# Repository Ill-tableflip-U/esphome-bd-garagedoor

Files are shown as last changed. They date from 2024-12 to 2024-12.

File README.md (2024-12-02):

# esphome B&D garage door configuration

This is how to build a complete pre-designed ESPhome device to interface with a B&D garage door, by simulating button presses on one of the included remotes (specifically a 2012 model)

Material list:
* 1 ESP32-C3 supermini
* A decent amount of wire
* A 5v/USB power source
* access to a 3d printer
optional:
* 1 ws2812 LED
* 1 hc-sr501 motion sensor
the B&D stock remote control can be opened up and modified for control use with ESPhome. for each garage door, the following is needed:
* 1 BC559 PNP transistor
* 1 10K ohm pullup resistor
* 1 1M ohm resistor for the base pin
* 1 reed switch (I recommend https://www.aliexpress.com/item/1005007038721944.html)
These all go inside the shell for the remote and can be directly soldered to it. Keep in mind, this likely only fits with the larger, white remote shells like the one pictured.

remote control modification


In the images, the blue wires are for power to hardwire the remote power along with the ESP. The red and white wires are the control outputs, for controlling the doors.
To modify the controller
1. eject the button cell battery as that will no longer be needed
2. straddle a BC559 transistor onto the side of the board for each button you wish to control. The collector pin should sit on the button solder pad closest to the board edge, meanwhile the emitter pin should be soldered to the pad closest to the center. The middle pin of the transistor (the base) should go onto the back side of the board. 

3. Solder a 1 million ohm resistor to the base pin of the BC559. (You should probably trim the legs of all of these)
4. after the 1m ohm resistor, solder one side of a 10k resistor to the empty end, and the other side to the button cell battery shieldd
5. Solder a ground wire to the 0v pad on the rear of the remote board and a 3.3v wire to the top of the button cell battery receptacle.
6. In the junction between the two resistors, solder a wire and connect it to any esp GPIO. You can now control your garage!

It is fairly easy to drill a small hole in the top of the original remote shell so these wires can be routed to the ESP setup.

Now, 3D print the enclosure for the device, or make your own. Mine, which has a .blend and a .stl available to print, has room for the the necessary hardware for garage doors as well as a ws2812 LED and a hc-SR501 motion sensor and is designed around the ESP32-C3 supermini. This is an effective all-in-one design that seems to work well.

PLEASE NOTE: some ESP32-C3 superminis have bad antenna chips, I used one of those for this project and it turned out fine. Still, YMMV.



Now, some basic reed switches can be plugged into the device through the holes in the sides. Make sure 1 pin is connected to ground, and the other to an IO pin. The reed switch should be placed, so that the circuit is closed when the garage door is closed. This will allow ESPhome and home assistant to detect whether the door is open or closed. It is a good idea to tape all your wires down so they don't get pulled out.



Now, change the example yaml I provided so that it has the correct pins for the sensors/outputs on your device. The example has the configuration for two garage doors.
This device can now simply be powered via a usb-c power source. Ensure the device works properly before mounting it.


For questions, feel free to open an issue.

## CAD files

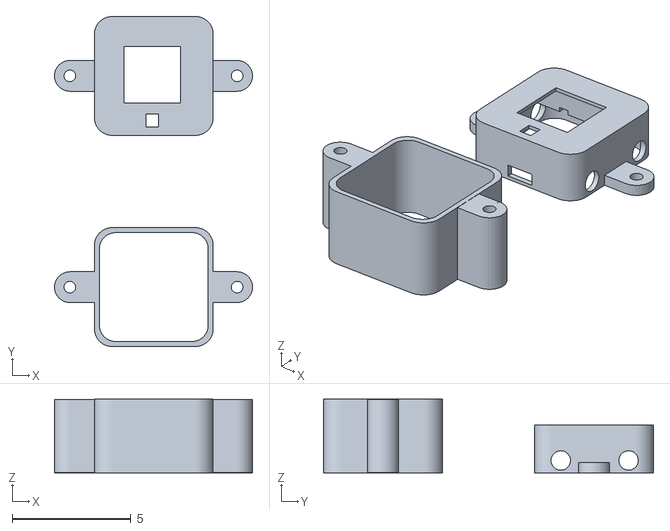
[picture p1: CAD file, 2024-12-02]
bd_garagedoorcontroller.stl
8.33 x 13.9 x 3.09

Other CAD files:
bd_garagedoorcontroller.blend

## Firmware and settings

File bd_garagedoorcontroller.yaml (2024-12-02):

esphome:
  name: garage-sensor
  friendly_name: Garage sensor

esp32:
  board: esp32-c3-devkitm-1
  framework:
    type: esp-idf
    sdkconfig_options: 
      CONFIG_BT_BLE_42_FEATURES_SUPPORTED: y
      CONFIG_BT_BLE_50_FEATURES_SUPPORTED: y
      CONFIG_ESP_TASK_WDT_TIMEOUT_S: "10"

# Enable logging
logger:
  baud_rate: 0
# Enable Home Assistant API
api:
  encryption:
    key: "xxxx"
  on_client_connected:
     - esp32_ble_tracker.start_scan:
        continuous: true
  on_client_disconnected:
    if:
      condition:
        not:
          api.connected:
      then:
        - esp32_ble_tracker.stop_scan:
esp32_ble_tracker:
  scan_parameters:
    # Don't auto start BLE scanning, we control it in the `api` block's automation.
    continuous: False
    
    active: True  # send scan-request packets to gather more info, like device name for some devices.

    interval: 320ms  # default 320ms - how long to spend on each advert channel
    window:   300ms  # default 30ms - how long to actually "listen" in each interval. Reduce this if device is unstable.
    # If the device cannot keep up or becomes unstable, reduce the "window" setting. This may be
    # required if your device is controlling other sensors or doing PWM for lights etc.
bluetooth_proxy:
  active: true  # allows outbound connections from HA to devices.

sensor:
  - platform: uptime
    # The uptime sensor is extremely helpful to know if your device is rebooting
    # when it shouldn't be. This might indicate your interval-to-window timing is
    # too tight, and the window needs to be reduced.
    name: "Uptime Sensor"
    update_interval: 60s
ota:
  - platform: esphome
    password: "xxxx"

wifi:
  ssid: !secret wifi_ssid
  password: !secret wifi_password
  manual_ip:
    # Set this to the IP of the ESP
    static_ip: 10.1.1.53
    # Set this to the IP address of the router. Often ends with .1
    gateway: 10.1.1.1
    # The subnet of the network. 255.255.255.0 works for most home networks.
    subnet: 255.255.255.0

  # Enable fallback hotspot (captive portal) in case wifi connection fails
  ap:
    ssid: "Garage-Sensor Fallback Hotspot"
    password: "xxxx"

captive_portal:
globals:
  - id: garage1moving
    type: bool
    restore_value: no
    initial_value: "false"
  - id: garage2moving
    type: bool
    restore_value: no
    initial_value: "false"
  

output:
  - platform: gpio
    id: garage1control
    pin: 10
    inverted: True
  - platform: gpio
    id: garage2control
    pin: 20
    inverted: True

light:
  - platform: esp32_rmt_led_strip
    chipset: ws2812
    id: status
    pin: 4
    num_leds: 1
    rmt_channel: 0
    rgb_order: GRB
binary_sensor:
  - platform: gpio
    pin: 21
    name: "Motion"
    device_class: motion
  - platform: gpio
    pin: 
      mode: 
        input: True
        pullup: True
      number: 2
      inverted: True
    id: garage1status
    name: Garage 1 closed
    
  - platform: gpio
    pin: 
      mode: 
        input: True
        pullup: True
      number: 7
      inverted: True
    id: garage2status
    name: Garage 2 closed
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
